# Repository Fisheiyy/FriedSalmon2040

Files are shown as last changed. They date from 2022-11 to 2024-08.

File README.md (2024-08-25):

# THIS PROJECT HAS BEEN ABANDONED

# FriedSalmon2040
 A RP2040 based 3D Printer Motherboard with 4 Integrated TMC2226 Stepper Drivers, PT1000 Support, 3 PWM Fans, 15A **Total** Heater Capability, 3 Expansion GPIO/3 Expansion Power IO

## [iBOM](https://htmlpreview.github.io/?https://github.com/Fisheiyy/FriedSalmon2040/blob/main/ibom.html), [BOM](https://docs.google.com/spreadsheets/d/18_6saM__RWSnnuOeO-IjOmcjcUNBl_MXiw4yVhhykyQ/edit#gid=1487594272), [Schematic](https://github.com/Fisheiyy/FriedSalmon2040/blob/main/rp2040-board.pdf) <br><br> Inspired by BigTreeTech SKR Mini E3 line <br> Made for the Voron & Klipper Communities
<hr>

# PICTURES
 ### V2 Development Picture
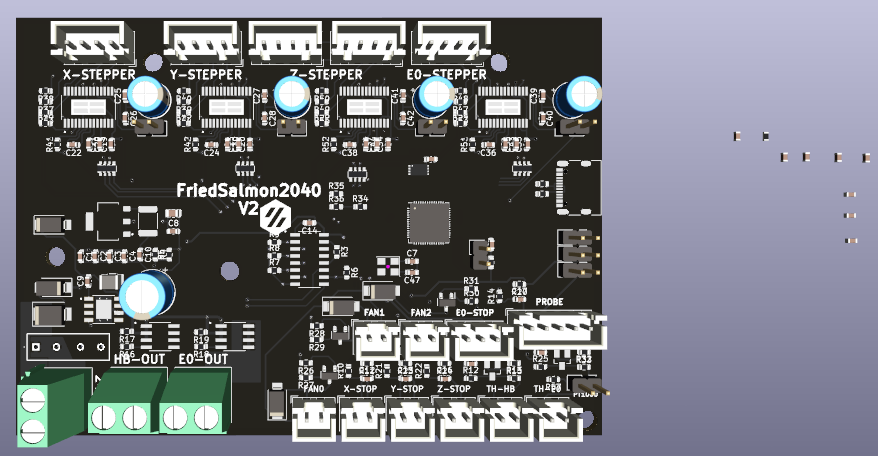
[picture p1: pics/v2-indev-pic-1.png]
FriedSalmon2040 V2 Indev Picture
 
<hr>

# LICENSE
 #### **You CANNOT use anything in this repo for Commercial Use without EXPLICIT PERMISSION**
*You can contact me if you have any questions regarding this.*
 ## This repository is under the [CC-BY-NC-SA-4.0](https://creativecommons.org/licenses/by-nc-sa/4.0) which states:
 ### You are free to:
   - Share — copy and redistribute the material in any medium or format
   - Adapt — remix, transform, and build upon the material
 ### Under the following terms:
  - Attribution — You **must** give **appropriate credit**, **provide a link to the license**, and **indicate if changes were made**. You may do so in any reasonable manner, but not in any way that suggests the licensor endorses you or your use.
  - NonCommercial — You may **not** use the material for **commercial purposes.**
  - ShareAlike — If you remix, transform, or build upon the material, you **must distribute your contributions under the same license as the original.**

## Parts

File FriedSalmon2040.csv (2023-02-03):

Source: | C:\Users\myall\Downloads\kicad projects\FriedSalmon2040\FriedSalmon2040.kicad_sch
Date: | 2/3/2023 12:51:42 AM
Tool: | Eeschema (6.0.11)
Generator: | C:\Program Files\KiCad\6.0\bin\scripting\plugins/bom_csv_grouped_by_value_with_fp.py
Component Count: | 178
Ref | Qnty | Value | Cmp name | Footprint | Description | Vendor
C1, C9, | 2 | 4.7uF | C_Small | Capacitor_SMD:C_0603_1608Metric | Unpolarized capacitor, small symbol
C2, C4, | 2 | 100nF | C_Small | Capacitor_SMD:C_0603_1608Metric | Unpolarized capacitor, small symbol
C3, | 1 | 1uF | C_Small | Capacitor_SMD:C_0603_1608Metric | Unpolarized capacitor, small symbol
C5, C8, C10, C12, C13, C14, C15, C16, C17, C18, C19, C20, C21, C23, C25, C26, C27, C28, C29, C30, C33, C34, C35, C37, C39, C40, C41, C42, C43, C44, C49, C50, C53, C54, C55, C56, C57, | 37 | 0.1uF | C_Small | Capacitor_SMD:C_0603_1608Metric | Unpolarized capacitor, small symbol
C6, | 1 | 22uF | C_Small | Capacitor_SMD:C_0805_2012Metric | Unpolarized capacitor, small symbol
C7, C47, | 2 | 10pF | C_Small | Capacitor_SMD:C_0603_1608Metric | Unpolarized capacitor, small symbol
C11, C58, C59, C60, | 4 | 22uF | C_Small | Capacitor_SMD:C_0603_1608Metric | Unpolarized capacitor, small symbol
C22, C24, C36, C38, | 4 | 22nF | C_Small | Capacitor_SMD:C_0603_1608Metric | Unpolarized capacitor, small symbol
C31, C32, C45, C46, | 4 | 100uF | C_Polarized_Small_US | Capacitor_THT:CP_Radial_D6.3mm_P2.50mm | Polarized capacitor, small US symbol
C48, C51, C52, | 3 | 2.2uF | C_Small | Capacitor_SMD:C_0603_1608Metric | Unpolarized capacitor, small symbol
C61, | 1 | 22pF | C_Small | Capacitor_SMD:C_0603_1608Metric | Unpolarized capacitor, small symbol
D2, | 1 | S5BBF | DIODE | Diode_SMD:D_SMB | Diode, anode on pin 1, for simulation only!
D4, D5, D6, | 3 | BAV99 | BAV99 | BAV99:DIO_BAV99
F1, | 1 | 20A | 01000063Z | 01000063Z:01000063Z | Fuse Clips FUSE HOLDER FOR MINIFUSE
J1, | 1 | 24V IN | Screw_Terminal_01x02 | TerminalBlock_Phoenix:TerminalBlock_Phoenix_MKDS-1,5-2_1x02_P5.00mm_Horizontal | Generic screw terminal, single row, 01x02, script generated (kicad-library-utils/schlib/autogen/connector/)
J2, | 1 | USB4105-GF-A | USB4105-GF-A | ul_USB4105-GF-A:USB4105-GF-A
J3, | 1 | CAN | Conn_01x02_Male | Connector_JST:JST_XH_B2B-XH-A_1x02_P2.50mm_Vertical | Generic connector, single row, 01x02, script generated (kicad-library-utils/schlib/autogen/connector/)
J4, | 1 | CHAM | Conn_01x02_Male | Connector_JST:JST_XH_B2B-XH-A_1x02_P2.50mm_Vertical | Generic connector, single row, 01x02, script generated (kicad-library-utils/schlib/autogen/connector/)
J5, | 1 | PROBE | Conn_01x05_Male | Connector_JST:JST_XH_B5B-XH-A_1x05_P2.50mm_Vertical | Generic connector, single row, 01x05, script generated (kicad-library-utils/schlib/autogen/connector/)
J6, | 1 | X-ENDSTOP | Conn_01x02_Male | Connector_JST:JST_XH_B2B-XH-A_1x02_P2.50mm_Vertical | Generic connector, single row, 01x02, script generated (kicad-library-utils/schlib/autogen/connector/)
J7, | 1 | BED | Conn_01x02_Male | Connector_JST:JST_XH_B2B-XH-A_1x02_P2.50mm_Vertical | Generic connector, single row, 01x02, script generated (kicad-library-utils/schlib/autogen/connector/)
J8, | 1 | Y-ENDSTOP | Conn_01x02_Male | Connector_JST:JST_XH_B2B-XH-A_1x02_P2.50mm_Vertical | Generic connector, single row, 01x02, script generated (kicad-library-utils/schlib/autogen/connector/)
J9, | 1 | Z-ENDSTOP | Conn_01x02_Male | Connector_JST:JST_XH_B2B-XH-A_1x02_P2.50mm_Vertical | Generic connector, single row, 01x02, script generated (kicad-library-utils/schlib/autogen/connector/)
J10, | 1 | E0-RUNOUT | Conn_01x03_Male | Connector_JST:JST_XH_B3B-XH-A_1x03_P2.50mm_Vertical | Generic connector, single row, 01x03, script generated (kicad-library-utils/schlib/autogen/connector/)
J11, | 1 | FAN0 | Screw_Terminal_01x02 | Connector_JST:JST_XH_B2B-XH-A_1x02_P2.50mm_Vertical | Generic screw terminal, single row, 01x02, script generated (kicad-library-utils/schlib/autogen/connector/)
J12, | 1 | FAN1 | Screw_Terminal_01x02 | Connector_JST:JST_XH_B2B-XH-A_1x02_P2.50mm_Vertical | Generic screw terminal, single row, 01x02, script generated (kicad-library-utils/schlib/autogen/connector/)
J13, | 1 | FAN2 | Screw_Terminal_01x02 | Connector_JST:JST_XH_B2B-XH-A_1x02_P2.50mm_Vertical | Generic screw terminal, single row, 01x02, script generated (kicad-library-utils/schlib/autogen/connector/)
J14, | 1 | HB | Screw_Terminal_01x02 | TerminalBlock_Phoenix:TerminalBlock_Phoenix_MKDS-1,5-2_1x02_P5.00mm_Horizontal | Generic screw terminal, single row, 01x02, script generated (kicad-library-utils/schlib/autogen/connector/)
J15, | 1 | E0 | Screw_Terminal_01x02 | TerminalBlock_Phoenix:TerminalBlock_Phoenix_MKDS-1,5-2_1x02_P5.00mm_Horizontal | Generic screw terminal, single row, 01x02, script generated (kicad-library-utils/schlib/autogen/connector/)
J16, | 1 | E0 | Conn_01x02_Male | Connector_JST:JST_XH_B2B-XH-A_1x02_P2.50mm_Vertical | Generic connector, single row, 01x02, script generated (kicad-library-utils/schlib/autogen/connector/)
J17, | 1 | X-STEPPER | Conn_01x04_Female | Connector_JST:JST_XH_B4B-XH-A_1x04_P2.50mm_Vertical | Generic connector, single row, 01x04, script generated (kicad-library-utils/schlib/autogen/connector/)
J18, | 1 | Y-STEPPER | Conn_01x04_Female | Connector_JST:JST_XH_B4B-XH-A_1x04_P2.50mm_Vertical | Generic connector, single row, 01x04, script generated (kicad-library-utils/schlib/autogen/connector/)
J19, | 1 | ZA-STEPPER | Conn_01x04_Female | Connector_JST:JST_XH_B4B-XH-A_1x04_P2.50mm_Vertical | Generic connector, single row, 01x04, script generated (kicad-library-utils/schlib/autogen/connector/)
J20, | 1 | E0-STEPPER | Conn_01x04_Female | Connector_JST:JST_XH_B4B-XH-A_1x04_P2.50mm_Vertical | Generic connector, single row, 01x04, script generated (kicad-library-utils/schlib/autogen/connector/)
J21, | 1 | ZB-STEPPER | Conn_01x04_Female | Connector_JST:JST_XH_B4B-XH-A_1x04_P2.50mm_Vertical | Generic connector, single row, 01x04, script generated (kicad-library-utils/schlib/autogen/connector/)
JP1, | 1 | RUN | Jumper_2_Open | Connector_PinHeader_2.54mm:PinHeader_1x02_P2.54mm_Vertical | Jumper, 2-pole, open
JP2, | 1 | X-DIAG | Jumper_2_Open | Connector_PinHeader_2.54mm:PinHeader_1x02_P2.54mm_Vertical | Jumper, 2-pole, open
JP3, | 1 | Y-DIAG | Jumper_2_Open | Connector_PinHeader_2.54mm:PinHeader_1x02_P2.54mm_Vertical | Jumper, 2-pole, open
JP4, | 1 | E0-DIAG | Jumper_2_Open | Connector_PinHeader_2.54mm:PinHeader_1x02_P2.54mm_Vertical | Jumper, 2-pole, open
JP5, | 1 | Z-DIAG | Jumper_2_Open | Connector_PinHeader_2.54mm:PinHeader_1x02_P2.54mm_Vertical | Jumper, 2-pole, open
JP6, | 1 | PT1000 | Jumper_2_Open | Connector_PinHeader_2.54mm:PinHeader_1x02_P2.54mm_Vertical | Jumper, 2-pole, open
L1, | 1 | 4.7uH | L_Small | Inductor_SMD:L_1210_3225Metric | Inductor, small symbol
Q1, Q2, Q3, | 3 | AO3400C | AO3400A | Package_TO_SOT_SMD:SOT-23 | 30V Vds, 5.7A Id, N-Channel MOSFET, SOT-23
R1, R12, R13, R25, R32, R61, | 6 | 2.37K | R_Small | Resistor_SMD:R_0603_1608Metric | Resistor, small symbol
R2, R3, R6, R7, R8, R9, R11, R20, R23, R24, | 10 | 10K | R_Small | Resistor_SMD:R_0603_1608Metric | Resistor, small symbol
R4, R63, | 2 | 25K | R_Small | Resistor_SMD:R_0603_1608Metric | Resistor, small symbol
R5, | 1 | 100K | R_Small | Resistor_SMD:R_0603_1608Metric | Resistor, small symbol
R10, R14, R21, R22, R34, R35, | 6 | 100R | R_Small | Resistor_SMD:R_0603_1608Metric | Resistor, small symbol
R15, R33, R57, R62, | 4 | 4.7K | R_Small | Resistor_SMD:R_0603_1608Metric | Resistor, small symbol
R16, R18, R26, R28, R30, | 5 | 10R | R_Small | Resistor_SMD:R_0603_1608Metric | Resistor, small symbol
R17, R19, R27, R29, R31, R37, R38, R39, R40, R41, R42, R47, R48, R49, R50, R51, R52, | 17 | 20K | R_Small | Resistor_SMD:R_0603_1608Metric | Resistor, small symbol
R36, R64, | 2 | 1K | R_Small | Resistor_SMD:R_0603_1608Metric | Resistor, small symbol
R43, R44, R45, R46, R53, R54, R55, R56, | 8 | 0.11R | R_Small | Resistor_SMD:R_0603_1608Metric | Resistor, small symbol
R58, R59, | 2 | 22R | R_Small | Resistor_SMD:R_0603_1608Metric | Resistor, small symbol
R60, | 1 | 200R | R_Small | Resistor_SMD:R_0603_1608Metric | Resistor, small symbol
RN1, RN2, RN3, RN4, | 4 | 100R | R_Pack03 | Resistor_SMD:R_Array_Convex_4x0603 | 3 resistor network, parallel topology
U1, | 1 | AMS1117-3.3 | AMS1117-3.3 | AMS1117-3.3:SOT229P700X180-4N
U2, | 1 | LM61460AANRJRR | LM61460AANRJRR | IC_LM61460AANRJRR
U3, | 1 | 74HCT365D,653 | 74HCT365D,653 | SOIC127P600X175-16N
U4, U5, | 2 | FDS8896 | FDS8896 | FDS8896:SOIC127P600X175-8N
U6, U7, U8, U9, | 4 | TMC2226-SA-T | TMC2226-SA-T | TMC2226:SOP65P640X120-29N
U10, | 1 | RP2040 | RP2040 | Package_DFN_QFN:QFN-56-1EP_7x7mm_P0.4mm_EP3.2x3.2mm | A microcontroller by Raspberry Pi
U11, | 1 | W25Q16JVUXIQ | W25Q80DVSNIG_TR | W25Q16JVUXIQ:SON50P300X200X60-9N
U12, | 1 | TJA1051TK-3 | TJA1051TK-3 | Package_DFN_QFN:DFN-8-1EP_3x3mm_P0.65mm_EP1.55x2.4mm | High-Speed CAN Transceiver, separate VIO, silent mode, DFN-8
Y1, | 1 | 12MHz | Crystal_GND24_Small | Oscillator:Oscillator_SMD_SeikoEpson_SG8002CE-4Pin_3.2x2.5mm | Four pin crystal, GND on pins 2 and 4, small symbol

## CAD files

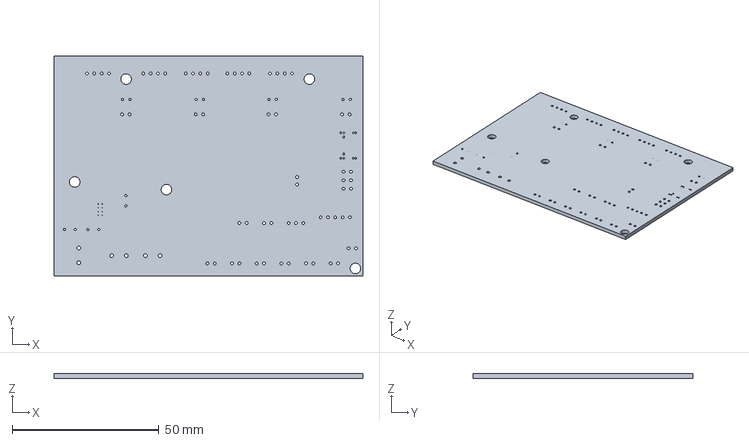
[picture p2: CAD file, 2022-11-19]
FriedSalmon2040.step
105.3 x 75.1 x 1.60 mm

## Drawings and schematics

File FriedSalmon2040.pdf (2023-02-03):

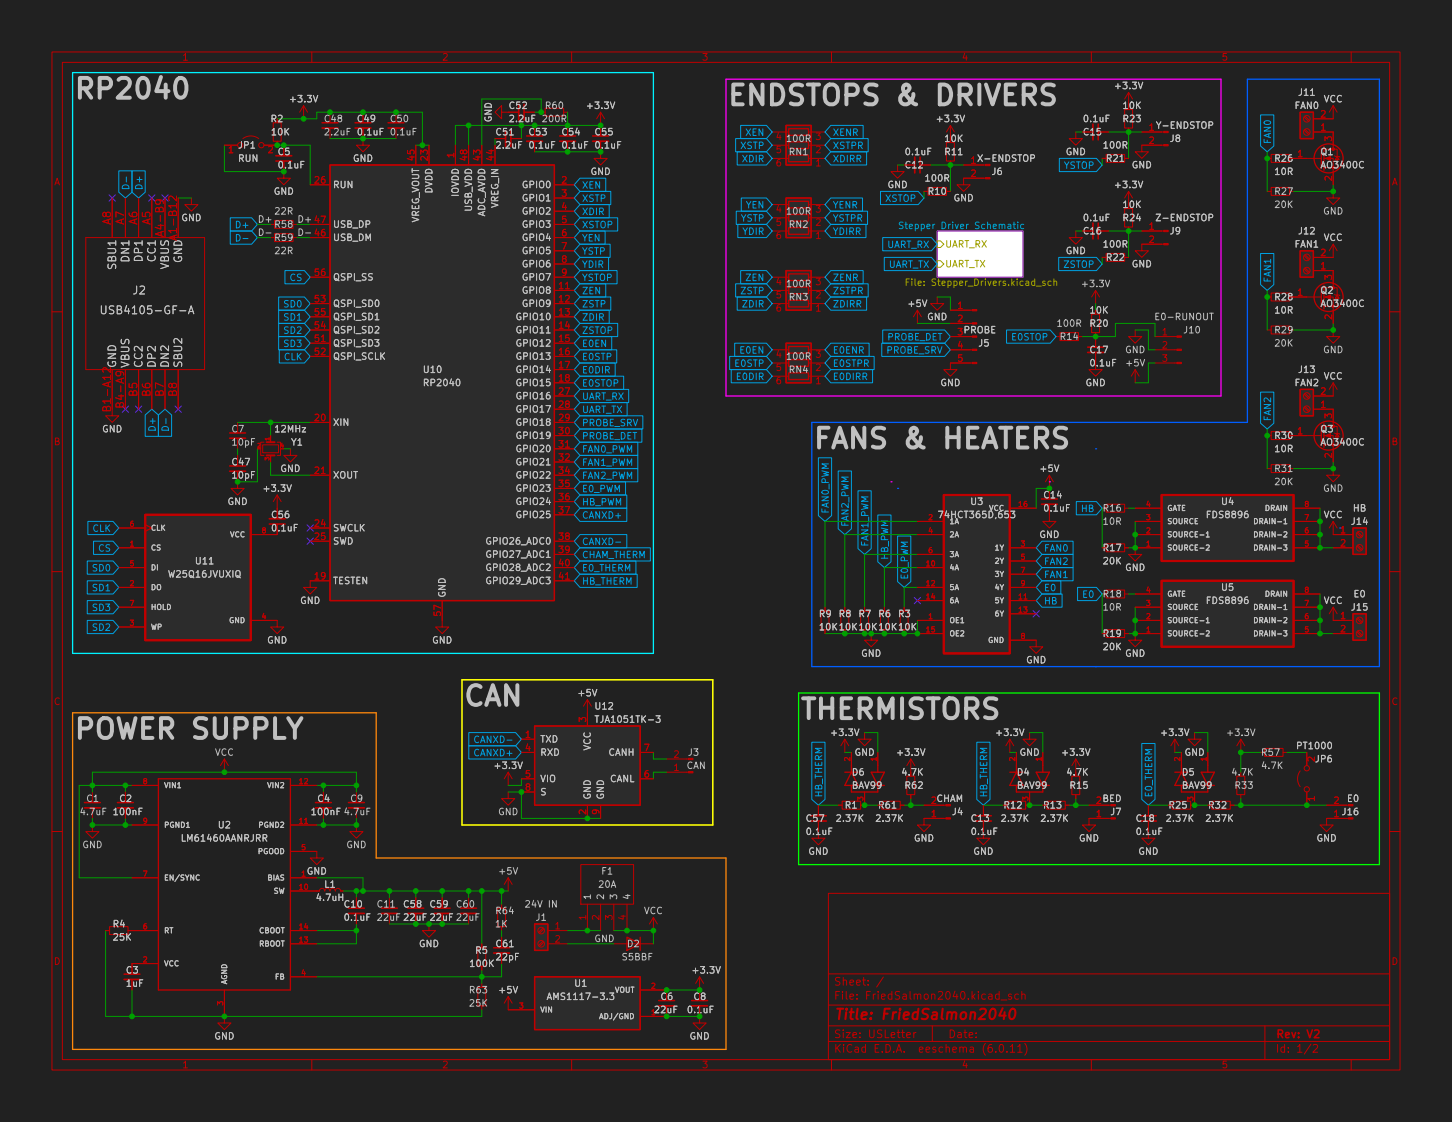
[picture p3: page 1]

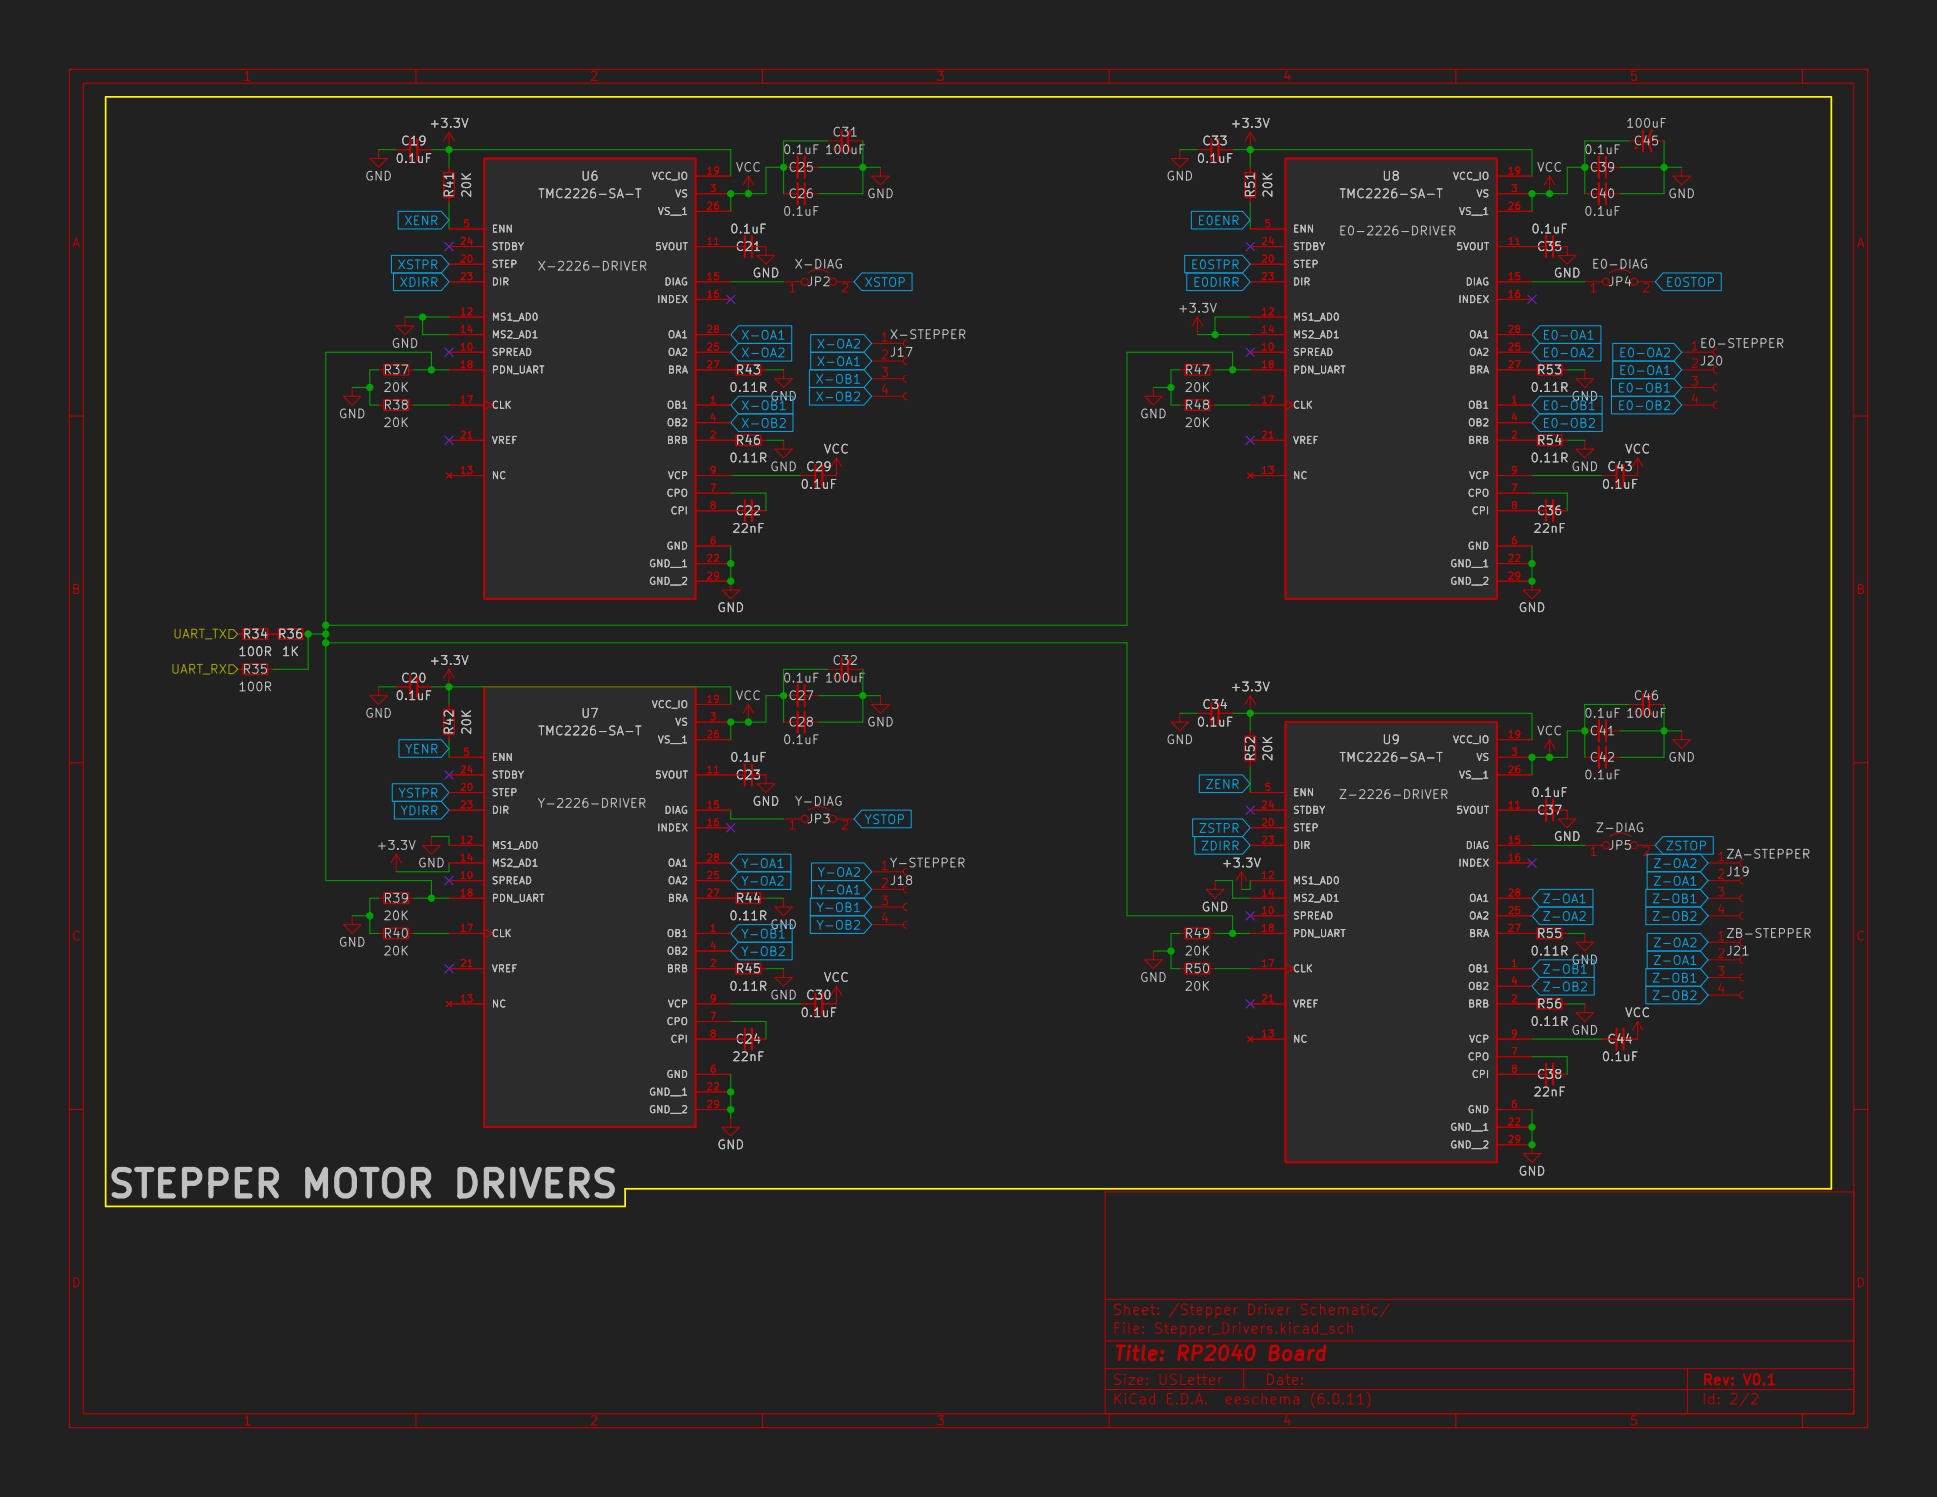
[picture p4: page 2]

Z-OA2 Z-2226-DRIVER STEPPER MOTOR DRIVERS

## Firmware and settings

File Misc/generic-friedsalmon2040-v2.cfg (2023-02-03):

# This file contains common pin mappings for the FriedSalmon2040.
# To use this config, the firmware should be compiled for the RP2040 with
# USB communication.

# The "make flash" command does not work on the FriedSalmon2040. Instead,
# after running "make", copy the generated "out/klipper.uf2" file
# to the mass storage device in RP2040 boot mode

# See docs/Config_Reference.md for a description of parameters.

[stepper_x]
step_pin: gpio1
dir_pin: !gpio2
enable_pin: !gpio0
microsteps: 16
rotation_distance: 40
endstop_pin: ^gpio3
position_endstop: 0
position_max: 235
homing_speed: 50

[tmc2209 stepper_x]
uart_pin: gpio16
tx_pin: gpio17
uart_address: 0
run_current: 0.580
stealthchop_threshold: 999999

[stepper_y]
step_pin: gpio5
dir_pin: !gpio6
enable_pin: !gpio4
microsteps: 16
rotation_distance: 40
endstop_pin: ^gpio7
position_endstop: 0
position_max: 235
homing_speed: 50

[tmc2209 stepper_y]
uart_pin: gpio16
tx_pin: gpio17
uart_address: 2
run_current: 0.580
stealthchop_threshold: 999999

[stepper_z]
step_pin: gpio9
dir_pin: gpio10
enable_pin: !gpio8
microsteps: 16
rotation_distance: 8
endstop_pin: ^gpio11
position_endstop: 0.0
position_max: 250

[tmc2209 stepper_z]
uart_pin: gpio16
tx_pin: gpio17
uart_address: 1
run_current: 0.580
stealthchop_threshold: 999999

[extruder]
step_pin: gpio13
dir_pin: !gpio14
enable_pin: !gpio12
microsteps: 16
rotation_distance: 33.500
nozzle_diameter: 0.400
filament_diameter: 1.750
heater_pin: gpio23
#sensor_type: PT1000
#pullup_resistor: 4700
sensor_type: EPCOS 100K B57560G104F
sensor_pin: gpio28
control: pid
pid_Kp: 21.527
pid_Ki: 1.063
pid_Kd: 108.982
min_temp: 0
max_temp: 250

[tmc2209 extruder]
uart_pin: gpio16
tx_pin: gpio17
uart_address: 3
run_current: 0.650
stealthchop_threshold: 999999

[heater_bed]
heater_pin: gpio24
sensor_type: EPCOS 100K B57560G104F
sensor_pin: gpio29
control: pid
pid_Kp: 54.027
pid_Ki: 0.770
pid_Kd: 948.182
min_temp: 0
max_temp: 130

#[temperature_sensor chamber]
#sensor_type: EPCOS 100K B57560G104F
#sensor_pin: gpio27
#min_temp: 0
#max_temp: 100
#gcode_id: chamber

[fan]
pin: gpio20

[heater_fan nozzle_cooling_fan]
pin: gpio21

#[heater_fan controller_fan]
#pin: gpio22

[mcu]
serial: /dev/serial/by-id/usb-Klipper_Klipper_firmware_12345-if00

[printer]
kinematics: cartesian
max_velocity: 300
max_accel: 3000
max_z_velocity: 5
max_z_accel: 100

#[bltouch]
#sensor_pin: gpio19
#control_pin: gpio18

#[filament_switch_sensor runout_sensor]
#switch_pin: ^gpio15

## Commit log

2022-07-14 Initial Upload - Mostly done Schematics
    help me I have no clue what im doing
    [rp2040-board.kicad_pcb, rp2040-board.kicad_sch, step_drv.kicad_sch]
2022-07-14 Finished Schematic
    [rp2040-board.kicad_sch, step_drv.kicad_sch]
2022-07-15 Misc & Update some components
    [step_drv.kicad_sch]
2022-07-21 Minor Schematic Layout Changes
    [rp2040-board.kicad_pcb, rp2040-board.kicad_sch, step_drv.kicad_sch]
2022-07-23 All components footprinted
    [rp2040-board.kicad_sch, step_drv.kicad_sch]
2022-07-23 BOM 99% done
    [rp2040-board.csv, rp2040-board.kicad_sch, step_drv.kicad_sch]
2022-07-25 Totally no 80% re-source of the BOM
    suuurely no re-source
    [rp2040-board.csv, rp2040-board.kicad_pcb, rp2040-board.kicad_sch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]
2022-08-05 almost done with layout...
    [rp2040-board.csv, rp2040-board.kicad_pcb, rp2040-board.kicad_sch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]
2022-08-10 I am in immense pain
    [rp2040-board.csv, rp2040-board.kicad_pcb, rp2040-board.kicad_sch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]
2022-08-30 so very close to done
    [rp2040-board.kicad_pcb]
2022-08-30 soooooooo close
    [rp2040-board.kicad_pcb]
2022-09-05 finished, for now, finally
    [rp2040-board-B_Cu.gbr, rp2040-board-B_Mask.gbr, rp2040-board-B_Paste.gbr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]
2022-09-05 Rev 1.1 - PT1000 + ADC/I2C GPIO
    [rp2040-board-B_Cu.gbr, rp2040-board-B_Mask.gbr, rp2040-board-B_Paste.gbr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]
2022-09-05 Change Inductor & PT1000 Resistor
    [rp2040-board-B_Cu.gbr, rp2040-board-B_Mask.gbr, rp2040-board-B_Paste.gbr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]
2022-09-06 minor edits, add klipper config
    [generic-friedsalmon2040-v1.1.cfg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]
2022-09-07 Update BOM + Minor PCB Touchups
    [rp2040-board-B_Cu.gbr, rp2040-board-B_Mask.gbr, rp2040-board-B_Paste.gbr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]
2022-09-08 Fix driver UART address configuration
    [rp2040-board-B_Cu.gbr, rp2040-board-B_Mask.gbr, rp2040-board-B_Paste.gbr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]
2022-09-20 add fan diodes + cleanup + copper fill clearances
    [rp2040-board-B_Cu.gbr, rp2040-board-B_Mask.gbr, rp2040-board-B_Paste.gbr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]
2022-11-19 Big updates, start of V2, actual RP2040
    change from V1.2 to V2 because of many optimizations to come
    [generic-friedsalmon2040-v1.1.cfg, generic-friedsalmon2040-v2.cfg, rp2040-board.kicad_pcb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]
2022-12-24 Updates, Move to 0602, Optimize Routing
    * 0805 -> 0602
    * Flash 8MB SOIC8 -> Flash 16MB USON 2x3
    * Indev Pic
    * Trace Optimization
    * Whatever else i forgor
    [rp2040-board.kicad_pcb, rp2040-board.kicad_sch, step_drv.kicad_sch]
2023-02-03 Renaming, Cleaning, Changing
    + TPS5450 -> LM61460
    = rp2040-board -> FriedSalmon2040
    + Cleanup tmc2226 layout
    + 3rd thermistor
    + CAN port
    give me a few more months...
    [FriedSalmon2040.csv, FriedSalmon2040.kicad_pcb, FriedSalmon2040.kicad_sch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]
